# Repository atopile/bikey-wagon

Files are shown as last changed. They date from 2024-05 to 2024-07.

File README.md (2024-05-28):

# A wagon for biking!

Love bikes? Wanna bring heavy stuff with you? This is the project for you!

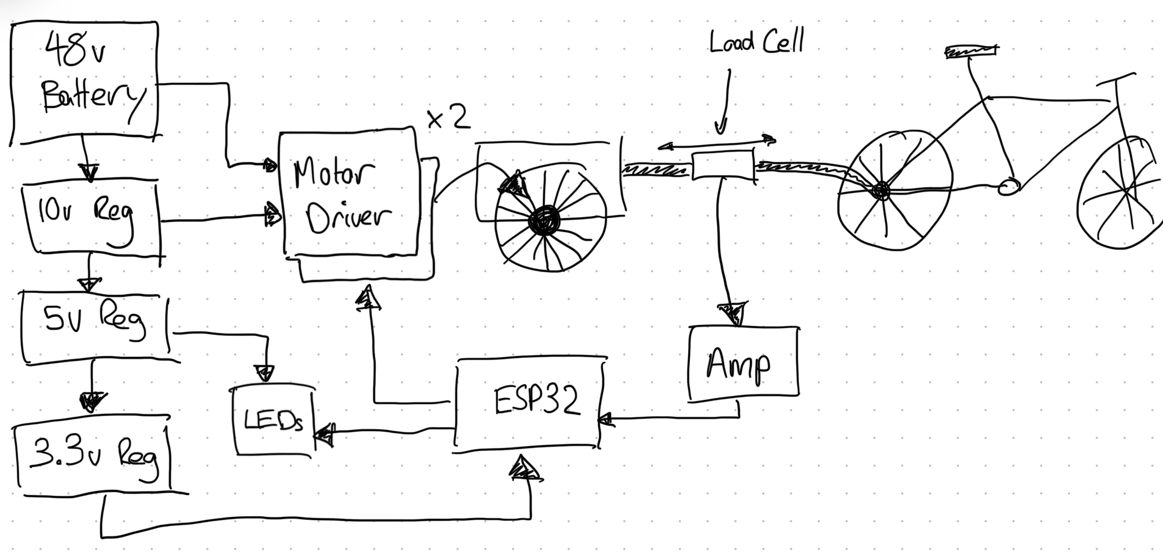
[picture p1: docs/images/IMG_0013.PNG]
block-view


## Goals

- Open-source project using atopile
- "Weightless" automatic control via load-cell
- 2x motor drivers + ESP32 for control

Come enjoy the ride on [Discord](https://discord.gg/2EWYghf8fr) or [YouTube](https://www.youtube.com/channel/UC8K4uNLYu_Vg9vLA_U93tVA)!

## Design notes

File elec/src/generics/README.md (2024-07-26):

# Generics

## Overview

Standard libaries for use in your projects. These include:

- **Resistors**
- **Capacitors**
- **Inductors**
- **Diodes**
- **Transistors**
- **Interfaces**

## Installation
Run in the terminal:

```
ato install generics
```

Add to your ato project:

- Resistors  `import Resistor from "generics/resistor.ato`
- Capacitors `import Capacitor from "generics/capacitor.ato`
- Inductors  `import Inductor from "generics/inductor.ato`
- Interfaces `import Interface from "generics/interface.ato`
- etc...

## Features
### Resistors
The standard libary includes several thousand resistor options. In your ato project, simply specify any requirements and the best resistor will be automatically selected.
Example:

```
import Resistor from "generics/resistor.ato"

myResistor = new Resistor
myResistor.value = 1000
myResistor.footprint = "R0402"
myResistor.tolerance = 10
```

The solver will find a resistor that has a resistance between 900 and 1100 ohms accounting for tolerance, and a footprint of R0402.

### Capacitors
Similar to resistors, just specify the value and footprint and the solver will find the best capacitor for your application.

### Inductors
Currently not supported for automatic selection, but you can install any inductor you like using `ato install` and then use it in your project.

We strongly reccomend using subclassing for new components, something like this:

```
import Inductor from "generics/inductor.ato"

component MyInductor from Inductor:
    value = 1000
    footprint = "L0402"
```

Then you can use it in your project like this:

```
import MyInductor from "myInductor.ato"

myInductor = new MyInductor
myInductor.value = 1000
myInductor.footprint = "L0402"
```

### Interfaces
Interfaces standardize the way you connect to modules. By implementing an interface from the standard libary, you can be sure that your module will be compatible with any other module that implements the same interface. This makes it easy to share modules between projects and be sure that they will work together.

## Contributing

We welcome contributions and suggestions to improve this module. Please submit your contributions as pull requests on our GitHub repository.

## License

This package documentation is provided under the [MIT License](#).

## Contact

For further inquiries or support, please contact us at [email@example.com](mailto:email@example.com).

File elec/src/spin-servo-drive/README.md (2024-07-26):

# Servos are dope.

Compared to the steppers we stick on our 3D printers, CNC machines and paintball turrets:
 - They're way faster 🏃
 - Far more powerful (higher torque for longer) 💪
 - More accurate (higher resolution) 🎯
 - And they're closed loop (they know where they are) 🤖

The only downside is that they're expensive, like hundreds of dollars.

Introducing spin ✨ - the $30 servo for the masses (designed with atopile)

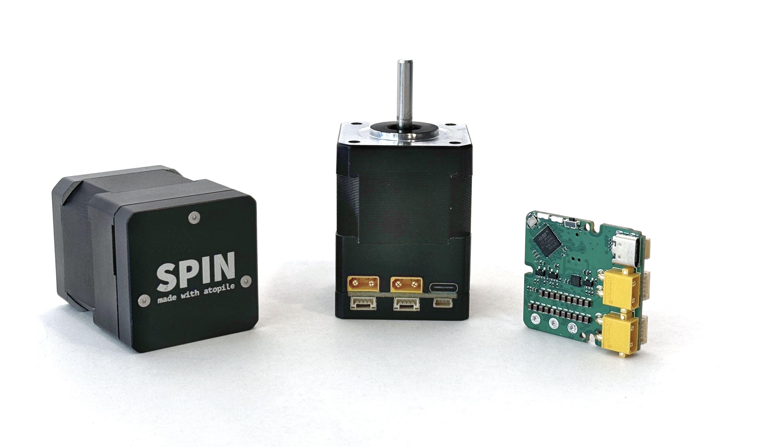
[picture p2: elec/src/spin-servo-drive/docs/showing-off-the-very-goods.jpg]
spin


## Wiggle wiggle wiggle

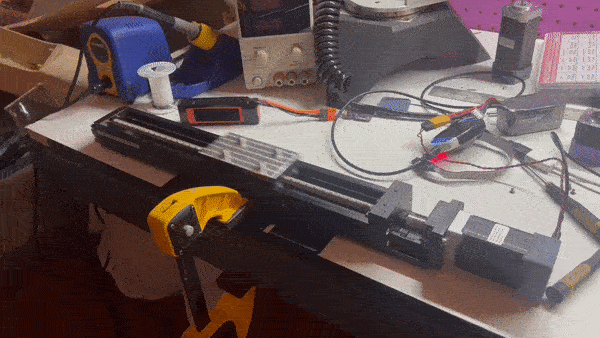
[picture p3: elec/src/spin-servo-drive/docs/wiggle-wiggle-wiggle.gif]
wiggle-wiggle-wiggle


## Goals + (default) Specs

- Obviously better option than stepper motors for 3D printers, CNC machines and robotics
- Open-source design that is easy to:
  - contribute to
  - fork maintainable derivatives of
  - robust

- 2x CAN comms with JST-GH connectors
- XT30 power connector
- 0.25Nm continuous rated torque (0.75Nm peak)
- <0.1° resolution
- 12V-24V input voltage

## Getting started

This project was written in `ato`, a new electronics description language we are developing to help create and share electronic designs. Get started here: https://atopile.io/getting-started

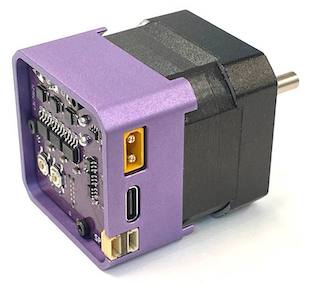
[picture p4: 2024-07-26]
elec/src/spin-servo-drive/docs/showing-off-the-goods.jpg

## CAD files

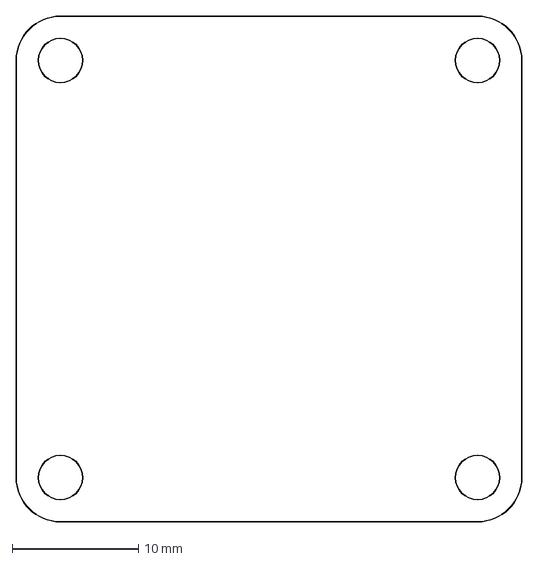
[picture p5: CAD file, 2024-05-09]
elec/src/spin-servo-drive/elec/src/programming-headers/mech/template_outline.dxf
40.0 x 40.0 mm

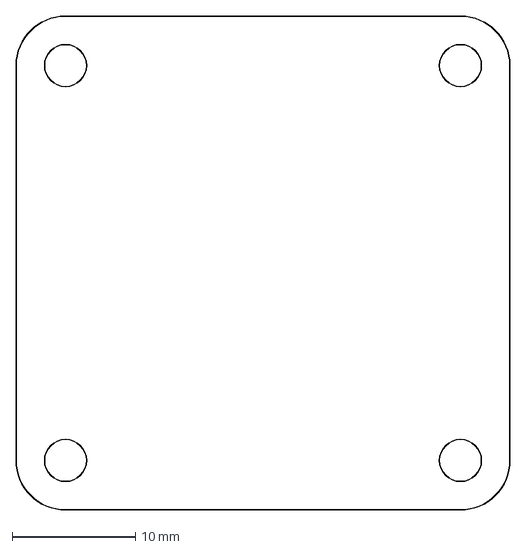
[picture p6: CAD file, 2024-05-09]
elec/src/spin-servo-drive/elec/src/saleae-header/mech/template_40x40.dxf
40.0 x 40.0 mm

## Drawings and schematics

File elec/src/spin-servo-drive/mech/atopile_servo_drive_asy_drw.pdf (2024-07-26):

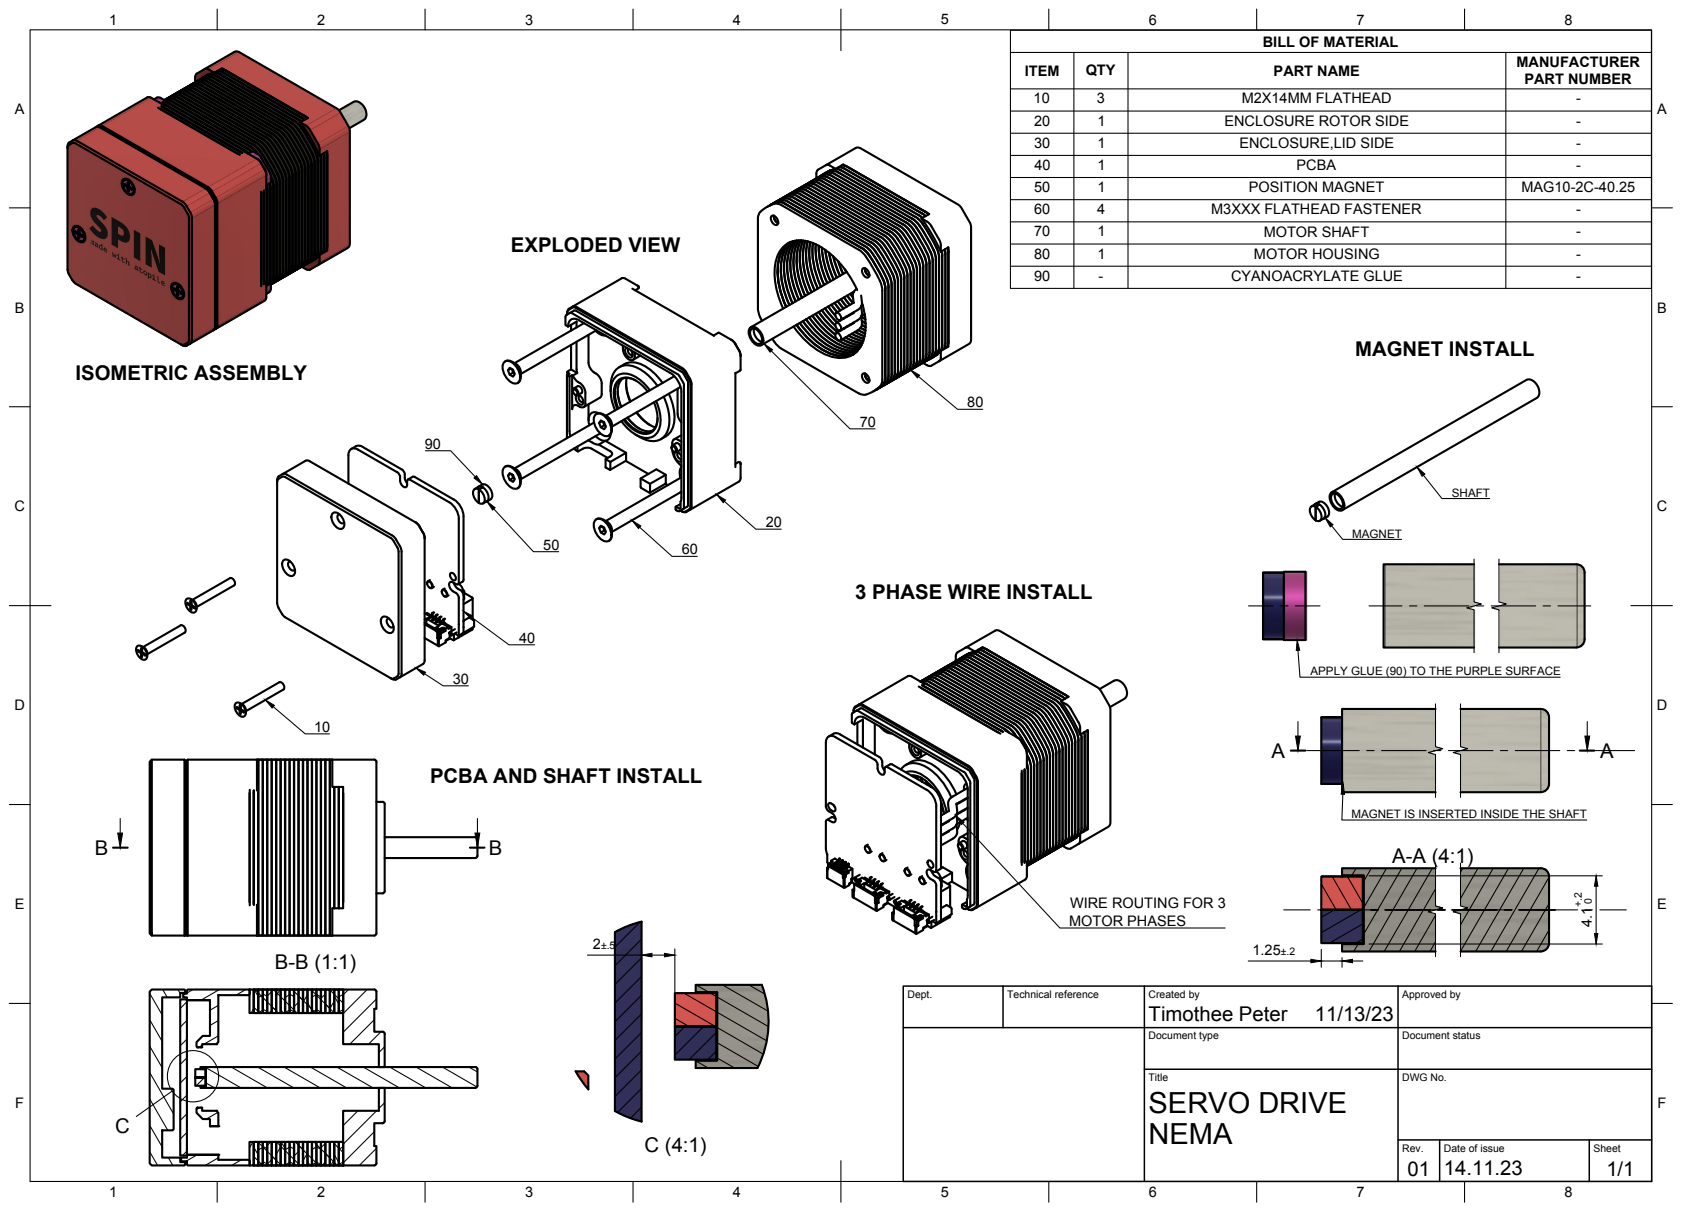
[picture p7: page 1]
Title; DWG No.; Rev.; Date of issue; Sheet; SERVO DRIVE; ITEM; QTY; PART NAME; MANUFACTURER; PART NUMBER; M2X14MM FLATHEAD; ENCLOSURE ROTOR SIDE; ENCLOSURE,LID SIDE; PCBA; POSITION MAGNET; MAG10-2C-40.25; M3XXX FLATHEAD FASTENER; MOTOR SHAFT; MOTOR HOUSING; CYANOACRYLATE GLUE; WIRE ROUTING FOR 3; MOTOR PHASES; MAGNET INSTALL; EXPLODED VIEW; ISOMETRIC ASSEMBLY

BILL OF MATERIAL

3 PHASE WIRE INSTALL

APPLY GLUE (90) TO THE PURPLE SURFACE

PCBA AND SHAFT INSTALL

MAGNET IS INSERTED INSIDE THE SHAFT

Dept. | Technical reference | Created by Timothee Peter 11/13/23 | Approved by

Document type | Document status

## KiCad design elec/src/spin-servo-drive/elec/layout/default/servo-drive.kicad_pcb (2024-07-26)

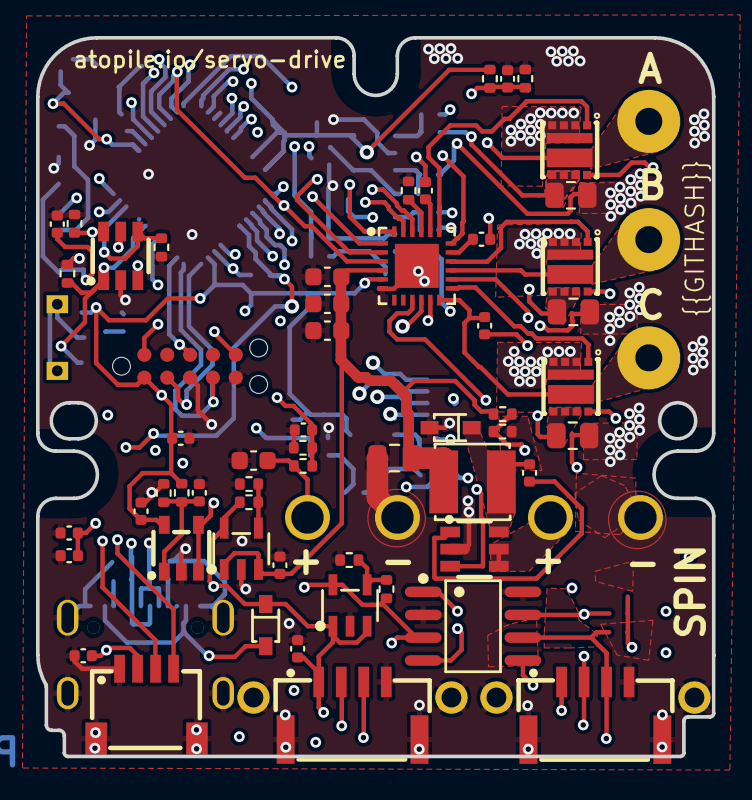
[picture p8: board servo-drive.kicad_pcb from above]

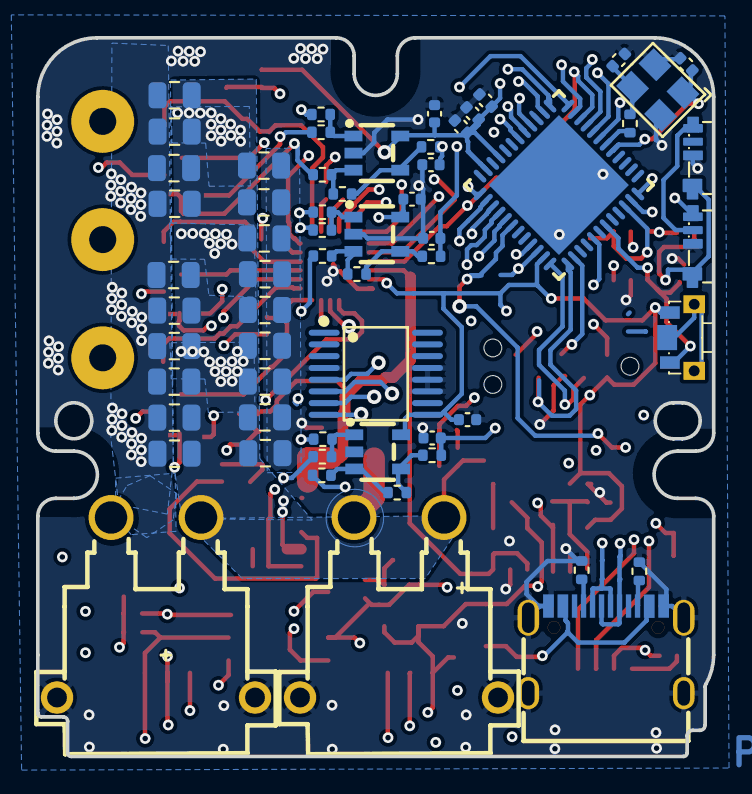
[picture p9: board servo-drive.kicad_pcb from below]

Board: 4 copper layers, 37.6 x 39.9 mm, 125 parts (60 on the bottom side), 80 nets.

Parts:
C1: 50V 1uF X5R ±10% 0603 Multilayer Ceramic Capacito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; C0603
C2, C13, C16, C17, C18, C19, C24, C28, C40, C51: 16V 100nF X7R ±10% 0402 Multilayer Ceramic Capaci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; C0402
C3, C4, C6, C20, C21, C22, C25, C26, C27, C29, C30, C35, C36, C37, C38, C39, C47, C48, C49: C0805
C5, C7, C9, C14, C15, C33, C34, C41, C43, C45, C50: 25V 1uF X5R ±10% 0402 Multilayer Ceramic Capacito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; C0402
C8: 25V 10uF X5R ±10% 0805 Multilayer Ceramic Capacit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; C0805
C10, C11, C12: 50V 2.2nF X7R ±10% 0402 Multilayer Ceramic Capaci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; C0402
C23, C31, C32: 16V 4.7uF X5R ±10% 0603 Multilayer Ceramic Capaci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; C0603
C42, C44: 50V 18pF C0G ±5% 0402 Multilayer Ceramic Capacito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; C0402
J1: USB-C-SMD_KH-TYPE-C-16P
R1, R15, R20, R38: 62.5mW Thick Film Resistors 50V ±100ppm/℃ ±1% 10k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; R0402
R2, R6, R13, R25, R44, R48, R50: 62.5mW Thick Film Resistors 50V ±100ppm/℃ ±1% 1kΩ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; R0402
R3: 62.5mW Thick Film Resistors 50V ±100ppm/℃ ±1% 100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; R0402
R4, R8, R47: R0805
R5, R9: 62.5mW Thick Film Resistors 50V ±100ppm/℃ ±1% 5.1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; R0402
R7: 62.5mW Thick Film Resistors 50V ±100ppm/℃ ±1% 220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; R0402
R10: 62.5mW Thick Film Resistors 50V ±100ppm/℃ ±0.5% 2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; R0402
R11: 62.5mW Thick Film Resistors 50V ±100ppm/℃ ±1% 3kΩ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; R0402
R12, R14, R26, R45, R49, R51: 62.5mW Thick Film Resistors 50V ±100ppm/℃ ±1% 47k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; R0402
R16, R46, R52: 62.5mW Thick Film Resistors 50V ±100ppm/℃ ±1% 73.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; R0402
R17: 62.5mW Thick Film Resistors 50V ±100ppm/℃ ±1% 20.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; R0402
R18: 62.5mW Thick Film Resistors 50V ±100ppm/℃ ±1% 6.3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; R0402
R19: 10kohm +/- 1%; R0402
R21: 62.5mW Thick Film Resistors 50V ±100ppm/℃ ±1% 11.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; R0402
R22: 62.5mW Thick Film Resistors 50V ±100ppm/℃ ±1% 6.2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; R0402
R29, R31: 62.5mW Thick Film Resistors 50V ±100ppm/℃ ±1% 41.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; R0402
R30: 62.5mW Thick Film Resistors 50V ±100ppm/℃ ±1% 4.3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; R0402
U1, U3, U28: V-DFN3030-8K_L3.0-W3.0-P0.65-BL
U2, U14: CONN-TH_XT30PW-M
U4, U20, U21, U24: SOT-23-5_L3.0-W1.7-P0.95-LS2.8-BR
U5, U32: LED-SMD_4P-L4.0-W1.4_SK6805SIDE-S
U6, U18: SOT-23-6_L2.9-W1.6-P0.95-LS2.8-BR
U7, U8, U9: OutputPad
U10: IND-SMD_L4.0-W4.0
U11: KEY-SMD_SKTDLDE010
U12: VQFN-24_L4.0-W4.0-P0.50-TL-EP2.5
U13: UFQFPN-48_L7.0-W7.0-P0.50-BL-EP
U15: CONN-SMD_4P-P1.00_SM04B-SRSS-TB-LF-SN
U16: TAG-CONNECT_TC2050-IDC
U17, U19, U31, U33, U34, U35: NetTie-2_SMD_Pad0.25mm
U22, U23: SOT-23-5_L3.0-W1.7-P0.95-LS2.8-BL
U25: SOIC-8_L4.9-W3.9-P1.27-LS6.0-BL
U26, U27: CONN-SMD_4P-P1.25_SM04B-GHS-TB-LF-SN
U29: TSSOP-16_L5.0-W4.4-P0.65-LS6.4-BL
U30, U36: SOD-323_L1.8-W1.3-LS2.5-RD
U37: OSC-SMD_4P-L3.2-W2.5-BL

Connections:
anchor: U11.3, U11.4
canh: U25.7, U26.2, U27.2
canl: U25.6, U26.3, U27.3
cb: C24.1, U6.1
cc1: J1.A5, R5.1
cc2: J1.B5, R9.1
cs: U13.25, U29.8
dm: J1.A7, J1.B7, U13.33
dp: J1.A6, J1.B6, U13.34
ios.led1-vcc: U5.3, U32.4
micro-miso: U13.27, U29.5
micro-mosi: U13.28, U29.6
micro-sda: U13.30, U15.3
micro-vcc: U5.4, U13.29
micro-vcc-1: R20.2, U11.1, U13.43, U18.1
micro-vcc-2: C28.1, R15.2, R19.1, U13.12
micro-vcc-3: C19.1, R10.2, R11.1, U13.13
micro.micro-io: R2.1, U13.46, U18.4
micro.micro-io-1: R3.1, U13.14, U18.6
micro.micro.ic-vcc-1: C42.1, U13.5, U37.1
pf1_osc_out: R7.1, U13.6
power_stage-gnd: C1.2, C2.2, C3.2, C4.2, C5.2, C6.2, C7.2, C8.2, C9.2, C10.2, C11.2, C12.2, C13.2, C14.2, C15.2, C16.2, C17.2, C18.2, C19.2, C20.2, C21.2, C22.2, C23.2, C25.2, C26.2, C27.2, C28.2, C29.2, C30.2, C31.2, C32.2, C33.2, C34.2, C35.2, C36.2, C37.2, C38.2, C39.2, C40.2, C42.2, C44.2, C47.2, C48.2, C49.2, C50.2, C51.2, J1.1, J1.2, J1.3, J1.4, J1.A1, J1.A12, J1.B1, J1.B12, R2.2, R3.2, R4.2, R5.2, R8.2, R9.2, R11.2, R18.2, R19.2, R20.1, R22.2, R30.2, R31.2, R38.2, R47.2, U2.1, U2.3, U2.4, U4.2, U5.2, U6.2, U12.6, U12.25, U13.49, U14.1, U14.3, U14.4, U15.1, U15.5, U15.6, U16.3, U16.5, U18.2, U19.2, U20.2, U21.2, U22.2, U23.2, U24.2, U25.2, U25.8, U26.4, U26.5, U26.6, U27.4, U27.5, U27.6, U29.4, U29.11, U29.12, U29.13, U32.2, U33.2, U35.2, U36.2, U37.2, U37.4
power_stage-vcc: C1.1, C3.1, C4.1, C6.1, C20.1, C21.1, C22.1, C25.1, C26.1, C27.1, C29.1, C30.1, C35.1, C36.1, C37.1, C38.1, C39.1, C47.1, C48.1, C49.1, R10.1, U1.2, U1.3, U1.4, U1.10, U2.2, U3.2, U3.3, U3.4, U3.10, U6.4, U6.5, U14.2, U28.2, U28.3, U28.4, U28.10
power_stage-vcc-1: C5.1, C8.1, C23.1, C31.1, C32.1, R29.1, U10.2, U12.4, U22.1, U22.3
power_stage-vcc-2: C7.1, C13.1, C15.1, C16.1, C17.1, C18.1, C40.1, C50.1, C51.1, R1.1, R15.1, R21.1, U4.5, U11.2, U12.5, U13.21, U13.23, U13.35, U13.48, U15.2, U16.1, U18.5, U20.5, U21.5, U23.5, U24.5, U25.3, U29.9
power_stage.gate_driver.ic-vcc: C41.1, U12.20
power_stage.gate_driver.ic-vcc-1: C43.1, U12.17
power_stage.gate_driver.ic-vcc-2: C45.1, U12.14
power_stage.gate_driver.ic-vcc-3: R31.1, U12.21
power_stage.phase_a-vcc: U12.1, U12.22, U13.8
power_stage.phase_a.current_sensor-vcc: R14.2, R45.2, R51.2, U4.3, U4.4
power_stage.phase_a.current_sensor-vcc-1: C10.1, R16.2, U13.17
power_stage.phase_a.current_sensor.bias_div-vcc: R13.1, U17.1
power_stage.phase_a.current_sensor.feedback_div-vcc: R6.1, U19.1
power_stage.phase_a.current_sensor.opamp-gnd: R12.2, R16.1, U20.4
power_stage.phase_a.current_sensor.opamp-inverting: R6.2, R12.1, U20.3
power_stage.phase_a.current_sensor.opamp-non_inverting: R13.2, R14.1, U20.1
power_stage.phase_a.half_bridge-gnd: R4.1, U17.2, U28.5, U28.6, U28.7
power_stage.phase_a.half_bridge-vcc: U12.19, U28.1
power_stage.phase_a.half_bridge-vcc-1: U12.11, U28.8
power_stage.phase_a.half_bridge-vcc-2: C41.2, U7.1, U12.18, U28.9
power_stage.phase_b-vcc: U12.2, U12.23, U13.9
power_stage.phase_b.current_sensor-vcc: C11.1, R46.2, U13.18
power_stage.phase_b.current_sensor.bias_div-vcc: R44.1, U31.1
power_stage.phase_b.current_sensor.feedback_div-vcc: R25.1, U33.1
power_stage.phase_b.current_sensor.opamp-gnd: R26.2, R46.1, U21.4
power_stage.phase_b.current_sensor.opamp-inverting: R25.2, R26.1, U21.3
power_stage.phase_b.current_sensor.opamp-non_inverting: R44.2, R45.1, U21.1
power_stage.phase_b.half_bridge-gnd: R8.1, U1.5, U1.6, U1.7, U31.2
power_stage.phase_b.half_bridge-vcc: U1.1, U12.16
power_stage.phase_b.half_bridge-vcc-1: U1.8, U12.10
power_stage.phase_b.half_bridge-vcc-2: C43.2, U1.9, U8.1, U12.15
power_stage.phase_c-vcc: U12.3, U12.24, U13.10
power_stage.phase_c.current_sensor-vcc: C12.1, R52.2, U13.11
power_stage.phase_c.current_sensor.bias_div-vcc: R50.1, U34.1
power_stage.phase_c.current_sensor.feedback_div-vcc: R48.1, U35.1
power_stage.phase_c.current_sensor.opamp-gnd: R49.2, R52.1, U24.4
power_stage.phase_c.current_sensor.opamp-inverting: R48.2, R49.1, U24.3
power_stage.phase_c.current_sensor.opamp-non_inverting: R50.2, R51.1, U24.1
power_stage.phase_c.half_bridge-gnd: R47.1, U3.5, U3.6, U3.7, U34.2
power_stage.phase_c.half_bridge-vcc: U3.1, U12.13
power_stage.phase_c.half_bridge-vcc-1: U3.8, U12.9
power_stage.phase_c.half_bridge-vcc-2: C45.2, U3.9, U9.1, U12.12
power_stage.voltage_reference.opamp-non_inverting: C2.1, R1.2, R38.1, U4.1
power_supply-vcc: J1.A4, J1.A9, J1.B4, J1.B9, U30.2
power_supply-vcc-1: C9.1, C14.1, C33.1, C34.1, R17.1, U5.1, U22.5, U23.1, U23.3, U26.1, U27.1, U30.1, U32.1
power_supply.buck.feedback_div-out: R29.2, R30.1, U6.3
power_supply.ldo3V3.feedback_div-out: R21.2, R22.1, U23.4
power_supply.ldo5V.feedback_div-out: R17.2, R18.1, U22.4
reset: U13.7, U16.10
rx: U18.3, U25.4
sck: U13.26, U29.7
scl: U13.16, U15.4
sw: C24.2, U6.6, U10.1, U36.1
tck: U13.37, U16.4
tdi: U13.38, U16.8
tdo: U13.41, U16.6
tms: U13.36, U16.2
tx: U13.47, U25.1
xout: C44.1, R7.2, U37.3

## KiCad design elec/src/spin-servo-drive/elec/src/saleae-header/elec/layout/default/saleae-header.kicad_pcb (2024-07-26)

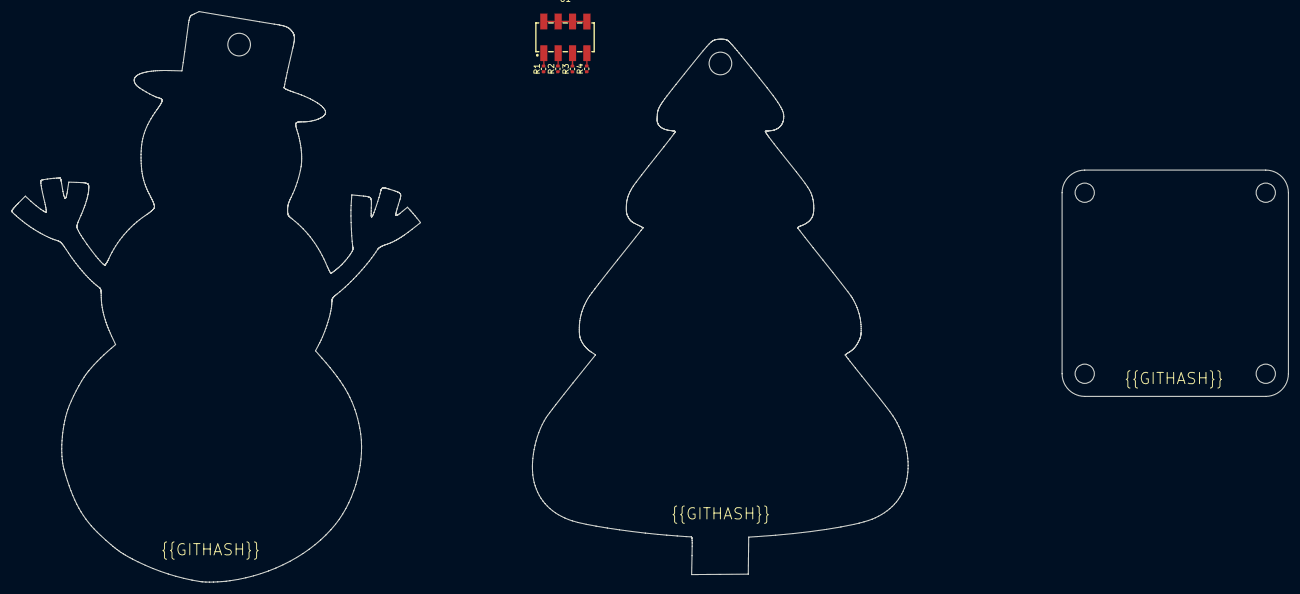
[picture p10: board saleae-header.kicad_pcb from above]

Board: 2 copper layers, 66.4 x 94.6 mm, 5 parts (0 on the bottom side), 5 nets.

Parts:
R1, R2, R3, R4: Chip Resistor - Surface Mount 1KOhms ±5% 1/16W 04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; R0402
U1: HDR-SMD_8P-P2.54-V-M-R2-C4-LS7.4

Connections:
_1: R1.2, U1.1
_3: R2.2, U1.3
_5: R3.2, U1.5
_7: R4.2, U1.7
gnd: U1.2, U1.4, U1.6, U1.8

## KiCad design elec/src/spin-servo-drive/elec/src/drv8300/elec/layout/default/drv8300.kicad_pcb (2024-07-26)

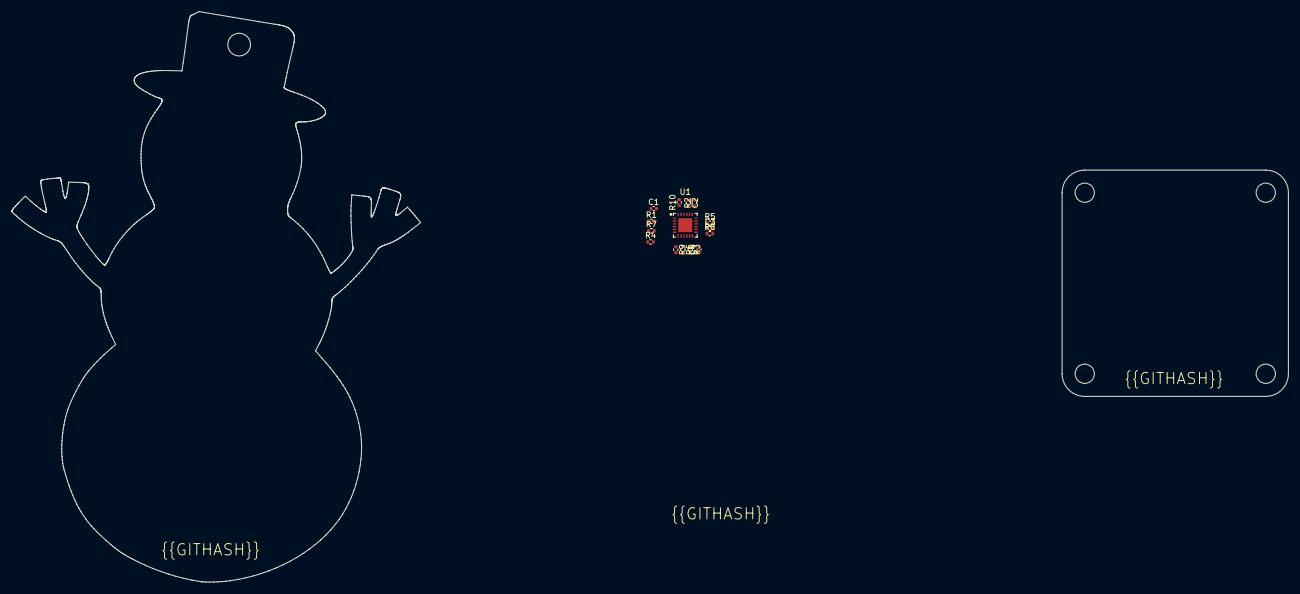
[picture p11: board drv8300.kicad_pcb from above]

Board: 2 copper layers, 15 parts (0 on the bottom side), 15 nets, no tracks yet.

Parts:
C1, C2, C3, C4: 25V 1uF X5R ±10% 0402 Multilayer Ceramic Capacito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; C0402
R1, R4, R7: Chip Resistor - Surface Mount 4.7KOhms ±5% 1/16W 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; R0402
R2, R3, R5, R6, R8, R9: Chip Resistor - Surface Mount 10Ohms ±5% 1/16W 04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; R0402
R10: Chip Resistor - Surface Mount 39KOhms ±5% 1/16W 0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; R0402
U1: VQFN-24_L4.0-W4.0-P0.50-TL-EP2.5

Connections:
gnd: R1.2, R4.2, R7.2, R10.2, U1.6, U1.25
gnd-9: C2.2, C3.2, C4.2, U1.20
vcc-1: U1.4, U1.5
vcc-6: U1.1, U1.22
vcc-7: C2.1, U1.18
vcc-8: R2.1, R2.2, U1.19
vcc-9: R3.1, U1.11
vcc-13: R10.1, U1.2, U1.23
vcc-14: C3.1, U1.15
vcc-15: R5.1, R5.2, U1.16
vcc-16: R6.1, U1.10
vcc-20: U1.3, U1.24
vcc-21: C4.1, U1.12
vcc-22: R8.1, R8.2, U1.13
vcc-23: R9.1, U1.9

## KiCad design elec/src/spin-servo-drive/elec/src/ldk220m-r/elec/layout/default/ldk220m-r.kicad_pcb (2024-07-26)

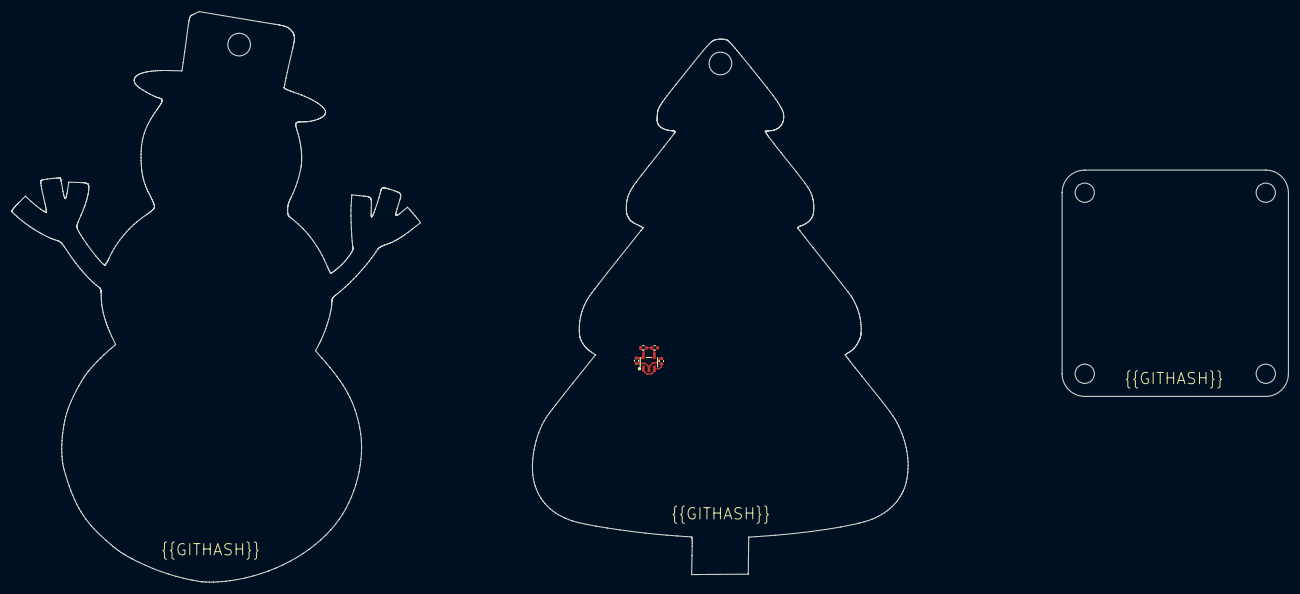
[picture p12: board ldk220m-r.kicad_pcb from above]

Board: 2 copper layers, 66.4 x 94.6 mm, 5 parts (0 on the bottom side), 4 nets.

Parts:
C1, C2: Multilayer Ceramic Capacitors MLCC - SMD/SMT 1uF 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; C0402
R1: Chip Resistor - Surface Mount 18KOhms ±5% 1/16W 0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; R0402
R2: Chip Resistor - Surface Mount 10KOhms ±5% 1/16W 0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; R0402
U1: SOT-23-5_L3.0-W1.7-P0.95-LS2.8-BL

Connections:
gnd: C1.2, C2.2, R2.2, U1.2
out: R1.2, R2.1, U1.4
vcc: C1.1, U1.1, U1.3
vcc-1: C2.1, R1.1, U1.5

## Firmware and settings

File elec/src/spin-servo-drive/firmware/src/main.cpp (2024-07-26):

#include <Arduino.h>
#include <SimpleFOC.h>
#include <SimpleFOCDrivers.h>
#include <Wire.h>

#include <settings/stm32/STM32FlashSettingsStorage.h>
#include <encoders/ma730/MagneticSensorMA730SSI.h>
#include <encoders/ma730/MagneticSensorMA730.h>
#include <encoders/hysteresis/HysteresisSensor.h>
#include <comms/telemetry/SimpleTelemetry.h>
#include <comms/telemetry/TeleplotTelemetry.h>
#include <utilities/stm32math/STM32G4CORDICTrigFunctions.h>


#define SERIAL_SPEED 115200


// TODO USB PD
// TODO current sense
// TODO voltage sense?
// TODO temperature sense?
// TODO CAN bus

// BLDC motor & driver instance
BLDCMotor motor = BLDCMotor(4, 2.0f, 300.0f);
BLDCDriver3PWM driver = BLDCDriver3PWM(PA0, PA1, PA2, PA3);

//Position Sensor
MagneticSensorMA730 sensor = MagneticSensorMA730(PB11);
HysteresisSensor hysteresisSensor = HysteresisSensor(sensor, 0.001f);

//LowsideCurrentSense current_sense = LowsideCurrentSense(0.003, 46, PB0, PB1, PB12);

// settings
STM32FlashSettingsStorage settings = STM32FlashSettingsStorage(); // use 1 page at top of flash

// instantiate the commander
Commander command = Commander(Serial);
void doMotor(char* cmd) { command.motor(&motor, cmd); };
void doSave(char* cmd) { settings.saveSettings(); };
void doLoad(char* cmd) { settings.loadSettings(); };
void doReinit(char* cmd) { motor.sensor_direction = Direction::UNKNOWN; motor.zero_electric_angle = NOT_SET; motor.initFOC(); };
void doHysteresis(char* cmd) { hysteresisSensor._amount = atof(cmd); Serial.print("Hysteresis: "); Serial.println(hysteresisSensor._amount, 4); };
void doSetSensor(char* cmd) {
  if (cmd[0]=='1') {
    motor.linkSensor(&hysteresisSensor);
    Serial.println("Using hysteresis");
  }
  else {
    motor.linkSensor(&sensor);
    Serial.println("Using MA730");
  }
};

// telemetry
TextIO textIO = TextIO(Serial);
//SimpleTelemetry telemetry = SimpleTelemetry();
TeleplotTelemetry telemetry = TeleplotTelemetry();
void doDownsample(char* cmd) { telemetry.downsample = atoi(cmd); };

void setup() {
  Serial.begin(SERIAL_SPEED);
  while (!Serial);
  SimpleFOCDebug::enable(&Serial);
  Serial.print("spin servo - firmware version ");
  Serial.println(SPIN_SERVO_FIRMWARE_VERSION);

  Wire.setSCL(PB8);
  Wire.setSDA(PB9);
  Wire.begin();
  Wire.setClock(400000);

  SPI.setMISO(PB14);
  SPI.setMOSI(PB15);
  SPI.setSCLK(PB13);

  SimpleFOC_CORDIC_Config();

  // driver config
  // power supply voltage [V]
  driver.voltage_power_supply = 10;
  driver.voltage_limit = driver.voltage_power_supply*0.95f;

  driver.init();
  sensor.init();
  hysteresisSensor.init();

  FieldStrength fs = sensor.getFieldStrength();
  Serial.print("Field strength: 0x");
  Serial.println(fs, HEX);

  // link driver
  motor.linkDriver(&driver);
  motor.linkSensor(&hysteresisSensor);

  // aligning voltage
  motor.voltage_sensor_align = 1;
  motor.current_limit = 2;
  motor.voltage_limit = driver.voltage_limit / 2.0f;
  motor.velocity_limit = 1000.0f; // 1000rad/s = aprox 9550rpm

  // some defaults
  motor.PID_velocity.P = 0.05f;
  motor.PID_velocity.I = 0.05f;
  motor.PID_velocity.D = 0.000f;
  motor.PID_velocity.output_ramp = 1000;
  motor.LPF_velocity.Tf = 0.01f;
  motor.P_angle.P = 20.0f;
  motor.P_angle.I = 0.0f;
  motor.P_angle.D = 0.0f;
  motor.P_angle.output_ramp = 1000;
  motor.LPF_angle.Tf = 0.005f;

  motor.torque_controller = TorqueControlType::voltage;
  motor.controller = MotionControlType::angle;
  motor.motion_downsample = 10;

  // load settings
  settings.addMotor(&motor);
  SimpleFOCRegister registers[] = { REG_SENSOR_DIRECTION, REG_ZERO_ELECTRIC_ANGLE, REG_VEL_LPF_T, REG_VEL_PID_P, REG_VEL_PID_I, REG_VEL_PID_D, REG_VEL_PID_LIM, REG_VEL_PID_RAMP, REG_ANG_LPF_T, REG_ANG_PID_P, REG_ANG_PID_I, REG_ANG_PID_D, REG_ANG_PID_LIM, REG_ANG_PID_RAMP, REG_CURQ_LPF_T, REG_CURQ_PID_P, REG_CURQ_PID_I, REG_CURQ_PID_D, REG_CURQ_PID_LIM, REG_CURQ_PID_RAMP, REG_CURD_LPF_T, REG_CURD_PID_P, REG_CURD_PID_I, REG_CURD_PID_D, REG_CURD_PID_LIM, REG_CURD_PID_RAMP, REG_VOLTAGE_LIMIT, REG_CURRENT_LIMIT, REG_VELOCITY_LIMIT, REG_MOTION_DOWNSAMPLE, REG_TORQUE_MODE, REG_CONTROL_MODE };
  settings.setRegisters(registers, sizeof(registers)/sizeof(SimpleFOCRegister));
  settings.settings_version = 2;
  settings.init();
  //settings.loadSettings();

  // initialize motor
  motor.init();

  // align sensor and start FOC
  Serial.print("Aligning...");
  motor.initFOC();

  // add commands
  command.echo = true;
  command.add('M', doMotor, "motor commands");
  command.add('s', doSave, "save settings");
  command.add('l', doLoad, "load settings");
  command.add('d', doDownsample, "downsample telemetry");
  command.add('r', doReinit, "reinit motor");
  command.add('h', doHysteresis, "hysteresis amount");
  command.add('S', doSetSensor, "set sensor (0=MA730, 1=hysteresis)");
  // add telemetry
  telemetry.addMotor(&motor);
  telemetry.downsample = 0; // off by default, use register 28 to set
  uint8_t telemetry_registers[] = { REG_TARGET, REG_ANGLE, REG_VELOCITY, REG_SENSOR_MECHANICAL_ANGLE, REG_ITERATIONS_SEC };
  telemetry.setTelemetryRegisters(sizeof(telemetry_registers)/sizeof(SimpleFOCRegister), telemetry_registers);
  telemetry.init(textIO);

  Serial.println(F("Motor ready."));
  Serial.println(F("Set the target using serial terminal:"));
}



void loop() {
  // Motion control function
  motor.move();
  // main FOC algorithm function
  motor.loopFOC();
  // user communication
  command.run();
  // telemetry
  telemetry.run();
}

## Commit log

2024-05-09 Configure project
    [the-wagon.kicad_pcb, the-wagon.kicad_sch]
2024-05-10 Not building yet, but a good demo of how a regulator can be designed
2024-05-15 Add implementation of a 3.3V supply
    [lmr16030buck-demo.kicad_pcb, lmr16030buck-demo.kicad_sch, lmr16030buck.kicad_pcb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]
2024-05-27 Configure power-stages and 10v supply
2024-07-19 Bring current feedback gains into range
2024-07-26 Hopefully this universally builds now
    [drv8300.kicad_pcb, drv8300.kicad_sch, jst-gh.kicad_pcb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]
